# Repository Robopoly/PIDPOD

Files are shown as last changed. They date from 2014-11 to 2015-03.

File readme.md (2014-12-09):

# PIDPOD

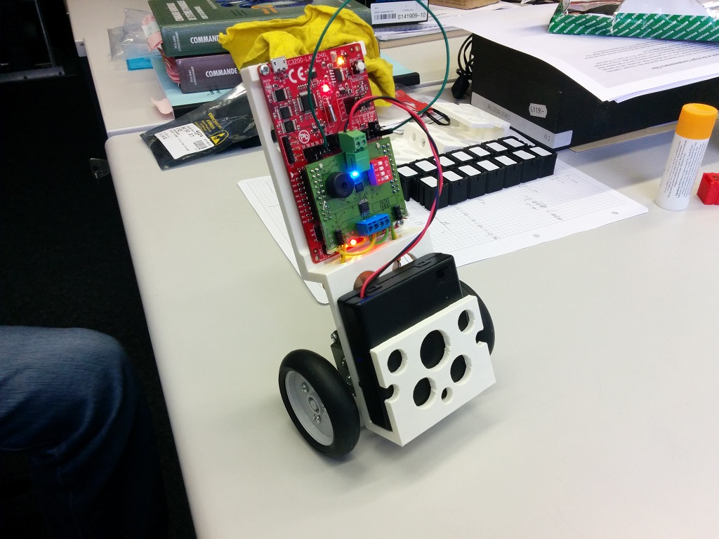
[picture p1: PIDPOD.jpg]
PIDPOD


The PIDPOD is a small self-balancing gyropod platform based on the Texas Instruments [CC3200 development board](http://www.ti.com/tool/cc3200-launchxl), a custom booster pack with additional electronics such as an inertial measurement unit (IMU) and some DC motors and wheels.

**[Watch the video of the PIDPOD in action](https://www.youtube.com/watch?v=XYrwYyiz-3s)**

## Scope statement

The PIDPOD was developed for the first Texas Instruments *Internet of Things (IoT)* workshop at [EPFL](http://www.epfl.ch/), organised by the university's robotics club: [Robopoly](http://robopoly.epfl.ch/) and [IEEE student branch](http://ieee.epfl.ch/) held on the 9th December 2014. The initiative to build the self-balancing platform was taken by Robopoly committee members and the whole project took less than 20 days from concept to product, most of the parts were readily available thanks to the robotics club parts stock.

The full scope statement was:

### Mechanical

* 2-wheeled
* 4-bay battery pack
* Upright structure
* Holes for the CC3200 development board

### Electronics (custom booster-pack)

* DRV8833 H-bridge with 100mOhm shunt resistors
* MPU9150 9-axis IMU
* Battery connector
* H-bridge connectors
* Buzzer
* 4-way DIP-switch
* LEDs
* Micromatch footprint for I2C
* Pins for input for odometry from IR sensors and encoders

### Software

* Generate PWM for motor control
* Use the on-board BMA222 accelerometer
* Interface and use the custom booster-pack IMU

### Bonus

If all main objectives from the main scope statement were satisfied before the workshop we would also implement some additional features:

* Current-control (torque) instead of voltage-control (speed) using the 100mOhm shunt and ADC
* Position control using encoders
* Set PID controller coefficients via Wi-Fi
* Interface a VGA camera (OV7670)

## Hardware

The PIDPOD uses the Tamiya double gearbox for the motors and the narrow tire set also from Tamiya, they were chosen because the were readily available at Robopoly.

For the power it uses 4 AA rechargeable batteries (4.8V total), this is partly because the LDO of the CC3200 development board requires a deltaV of 1V minimum for the 3.3V regulator and also for motor power. Although the motors should not exceed 3V we assume the system will stay at extremes for short times only.

The chassis was 3D printed on an Ultimaker 2, it's a single piece with full of holes to make the structure lighter. It holds together the electronics, motors and the battery-pack.

At first the battery pack was on top of the chassis for accessibility, but the Tamyia motors were not powerful or fast enough to stabilise the system so the battery pack was lowered to the wheel axis level, the system performed much better and the motors were definately good enough for a gyropod in this configuration.

## Electronics

The additional electonic components on the custom booster pack are: an H-bridge (DRV8833), a 9-axis IMU (MPU9150), a buzzer and a 4-way DIP-switch and various connectors.

The CC3200 development board has an accelerometer ([BMA222](http://www.bosch-sensortec.com/en/homepage/products_3/3_axis_sensors/acceleration_sensors/bma222_1/bma222)), but we found out quickly that for a good regulation a gyroscope was needed, we never succeeded in achieving stability with only an accelerometer, thus the MPU9150 on the booster pack. The MPU9150 comes in an LGA package impossible to solder by hand, thanks to the [EPFL ACI workshop](http://sti-ateliers.epfl.ch/page-19942.html), and more specifically André Badertscher, we were able solder this part with ease.

The custom booster-pack was made possible by the ACI workshop and generously manufactured thanks to Manuel Leitos, they were very kind to produce a couple PCBs for us in a very short time allowing us to make this project.

## Software

For software development we had to start by developing the PWM signal generation for motor control, we used interrupt vectors instead of hardware PWM of the CC3200 chip, in retrospective the overhead that the pin settings take is quite annoying and in an eventual next version hardware PWM should be implemented.

We found out quite fast that the on-board BMA222 accelerometer was not enough to stabilise the system, fortunately we had prepared the footprint for the MPU9150 9-axis IMU that had a 3-axis gyroscope.

By the end of the project we had a Wi-Fi enabled gyropod on which we could set the PID controller coefficients using sliders via a server running on the CC3200.

## Issues

* Stability: the PIDPOD isn't very stable as we had to hand-tune the PID coefficients because of lack of time.
* Program: the program has some non-identified erratic behaviours sometimes, we did not investigate any further as we had something that somehow worked just before the deadline.
* I2C: when the motors pulled a lot of current the I2C communication stopped with the BMC222, it turns out the traces going to the unsoldered MPU9150 were somehow affecting the bus, we brutally cut the traces and everything worked from the onwards. We used the MPU9150 IMU later on and we did not have this issue.
* Wi-Fi: sometimes when the motors pull a lot of current the Wi-Fi communication stops.
* Memory: the CC3200 had some example programs stored in the flash memory limiting the user program size to less than 50Kb, the program needed more and thus we had to find a way to use the full theoretical 256Kb. For this there was a tool to format the memory (UniFlash), but no matter what we tried the tool refused to format the chip. In the end we found out that we needed to connect the SOP2 jumpter, exactly the contrary to the formatting instructions.
* Reset: the reset button on our CC3200 development board didn't work (the button did not short when pushed), we resorted to shorting it manually with a wire when we needed a reset.
* Current-control: reading the analog values for curren-control did not work as expected so we abandoned this idea.
* Camera: there was no way to interface the camera and have all the other functionalities we needed on the custom booster-pack as it took up too many pins, so we didn't put the camera footprint on it.
* FTDI: at one point the CC3200 decided to make the PC load new drivers and enumerated as 2 serial ports, the CC3200 became impossible to reprogram via Code Composer or Energia, it was still flashable via the UniFlash tool. We fixed this issue by reflashing the FTDI chip.

# Credits

This project was developed by Marco Pagnamenta, Karl Kangur and Jean-Luc Liardon, members of the Robopoly committee and former students of EPFL.

A huge thanks to Manuel Leitos and André Badertscher from ACI workshop who made the development of the electronics possible.

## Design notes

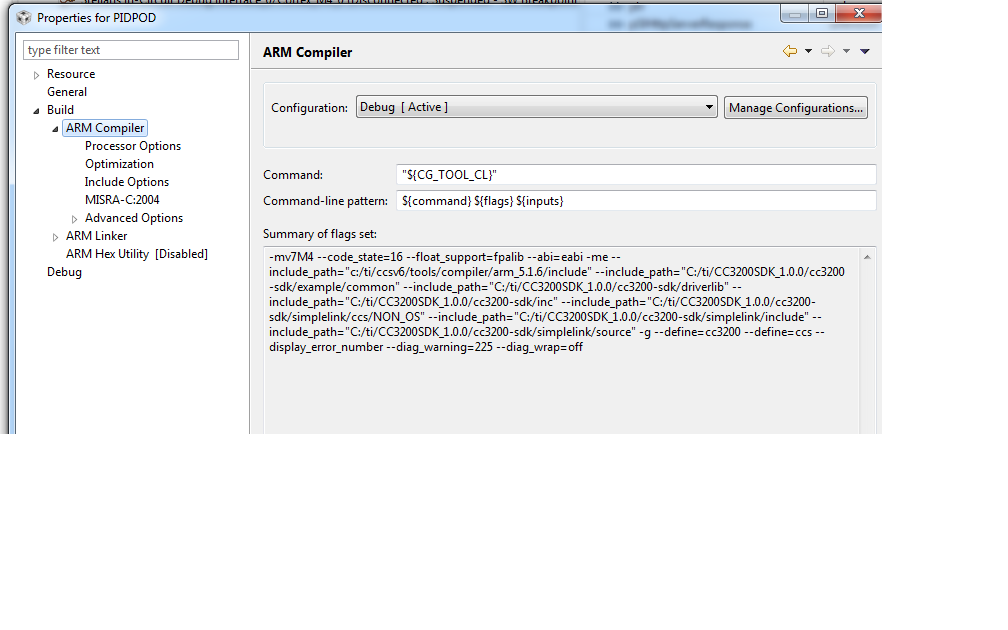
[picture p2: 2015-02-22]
CCS_project_options_screenshots/compiler_flags.png

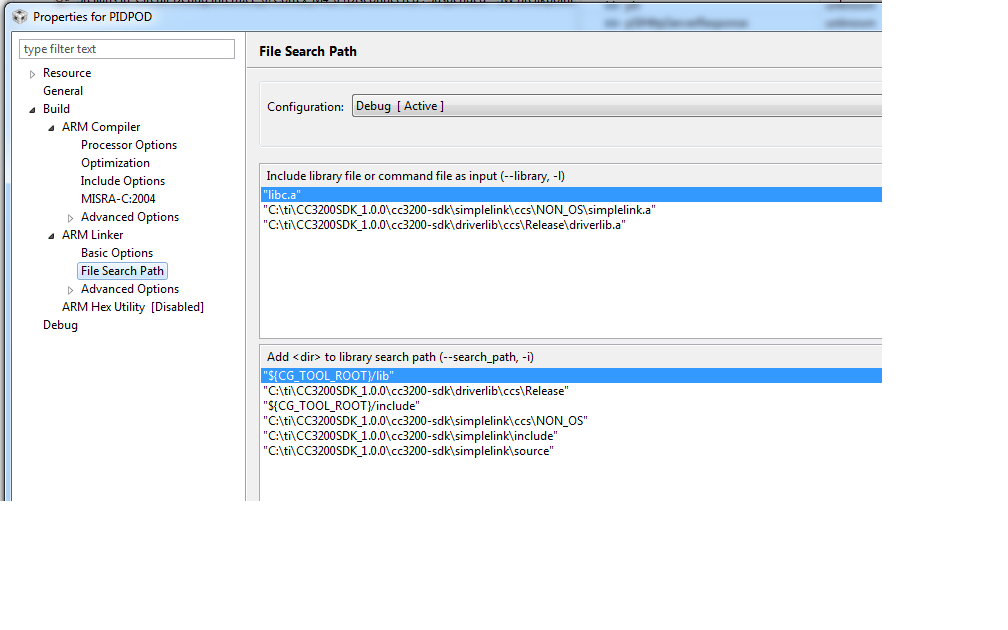
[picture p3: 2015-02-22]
CCS_project_options_screenshots/linker_search_path.png

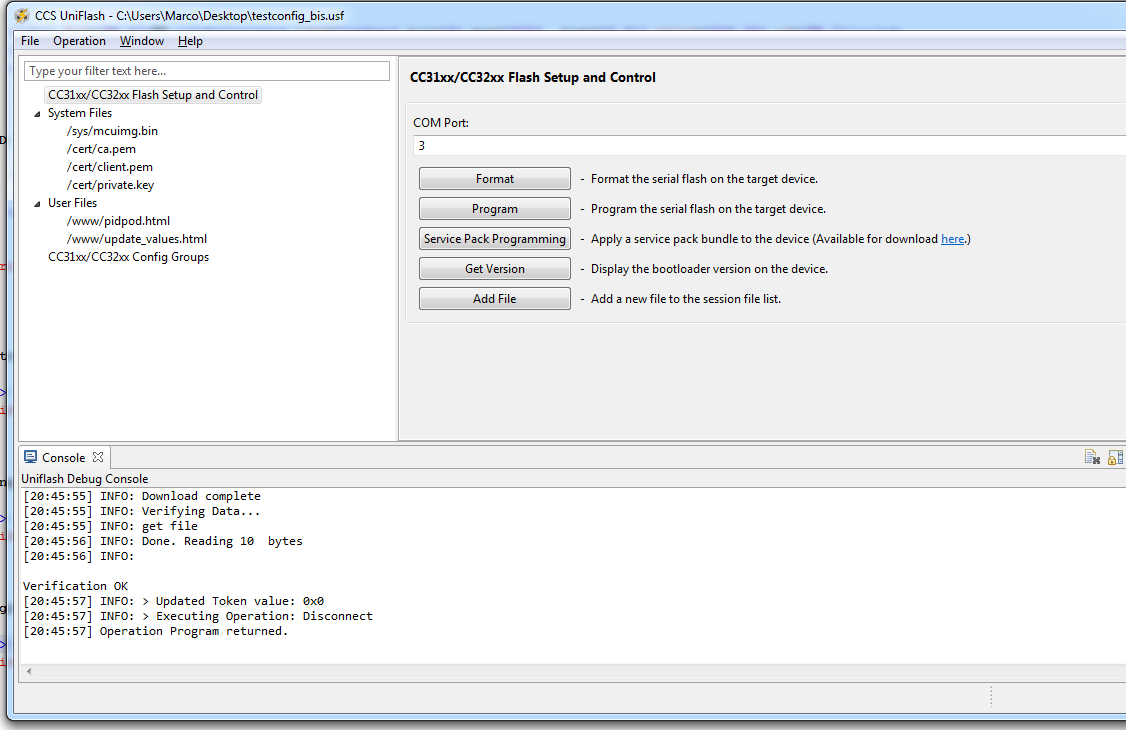
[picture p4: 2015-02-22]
CCS_project_options_screenshots/uniflash_settings.png

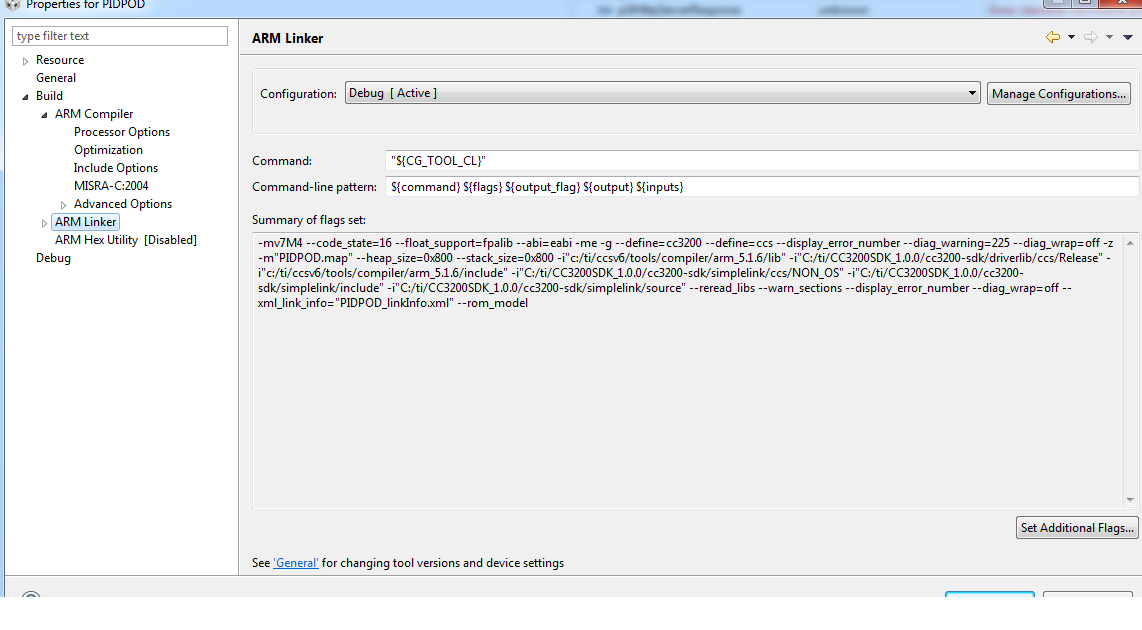
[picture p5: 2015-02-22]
CCS_project_options_screenshots/linker_flags.png

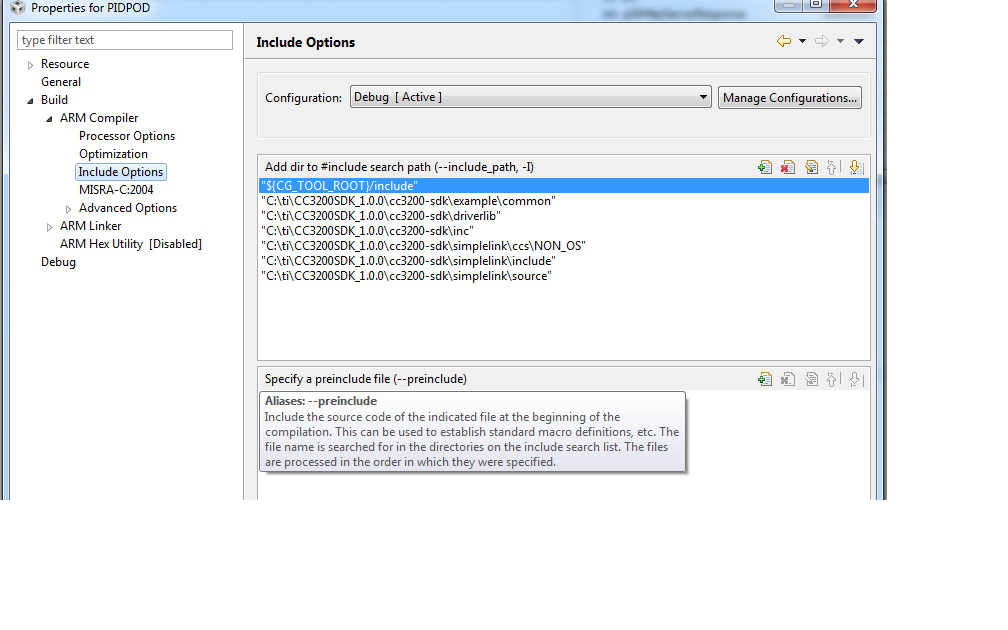
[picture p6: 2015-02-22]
CCS_project_options_screenshots/compiler_includes.png

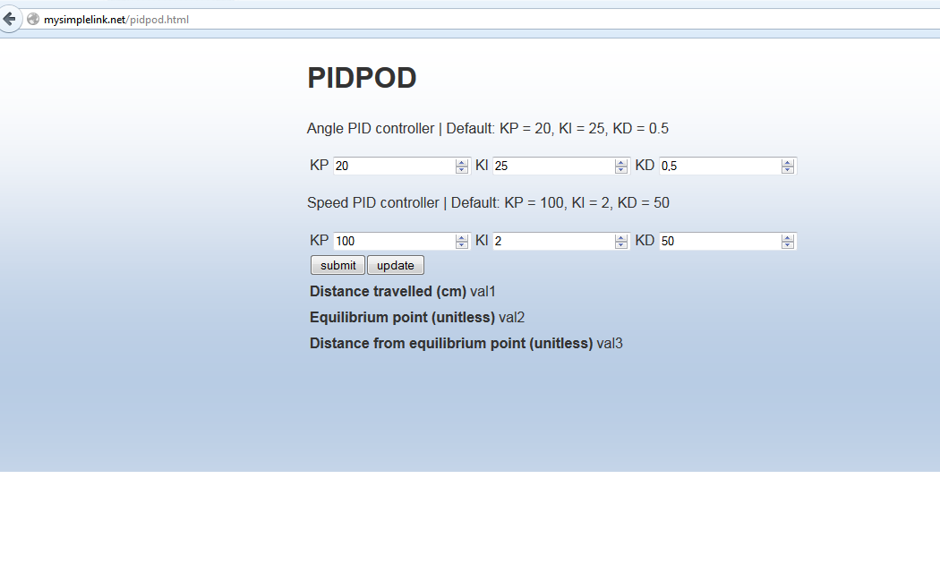
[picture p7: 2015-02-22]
CCS_project_options_screenshots/webpage.png

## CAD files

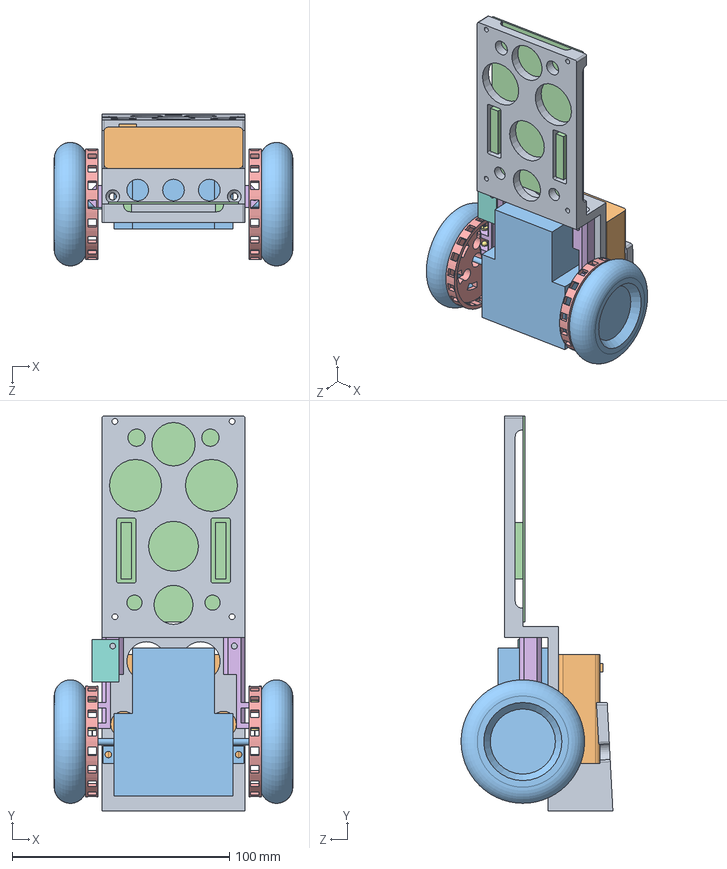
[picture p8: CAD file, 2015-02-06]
Hardware_v2/Assembly3.SLDASM
110.0 x 182.0 x 69.9 mm
Base_v3
Batteries
Wheels
CC3200
odometer3D x 2
IR_holder x 2
IR_transducer x 4
IR_PCB

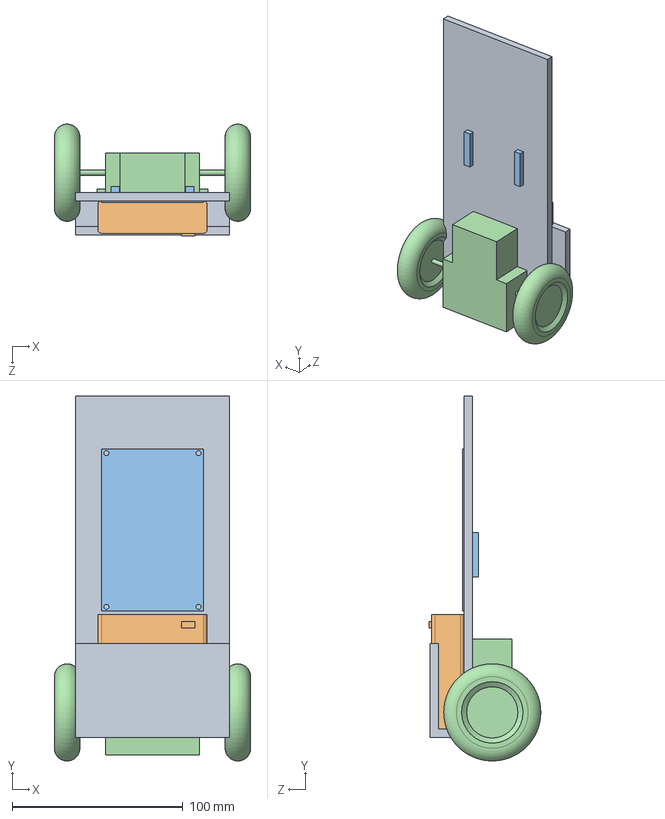
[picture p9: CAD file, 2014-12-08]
Hardware_v2/Assembly2.SLDASM
115.0 x 213.8 x 65.5 mm
Base_v2
Batteries
CC3200
Wheels

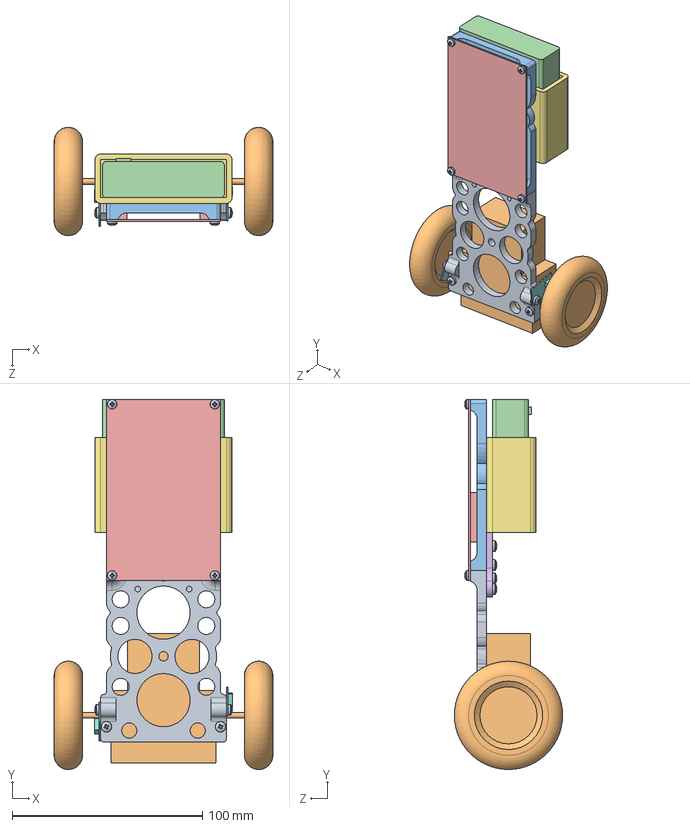
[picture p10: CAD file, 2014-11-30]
Hardware_v2/Assembly.SLDASM
115.0 x 194.5 x 56.9 mm
Base
Wheels
Top
Batteries
CC3200
Support
Battery support
ir_tcrt1000 x 2
pan head cross recess screw_iso x 15
hex nut style 1 gradeab_iso x 2
countersunk flat head cross recess screw_iso x 3

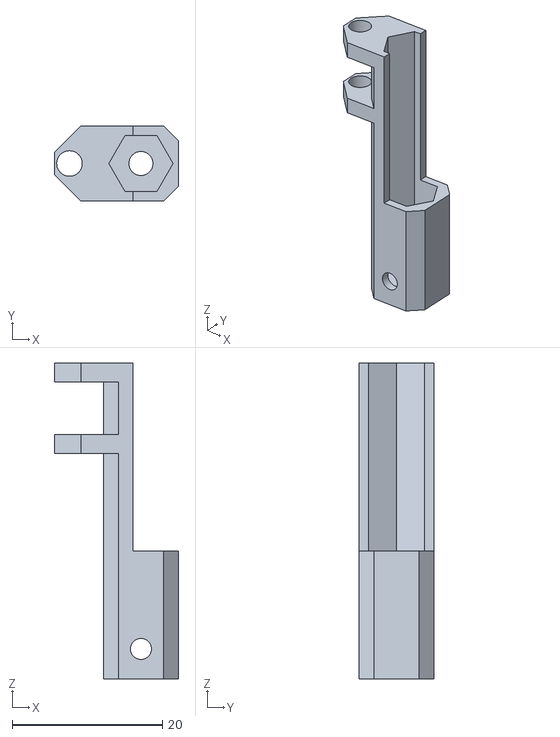
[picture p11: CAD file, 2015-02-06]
STL files/IR_holder.STL
16.5 x 10.0 x 42.0

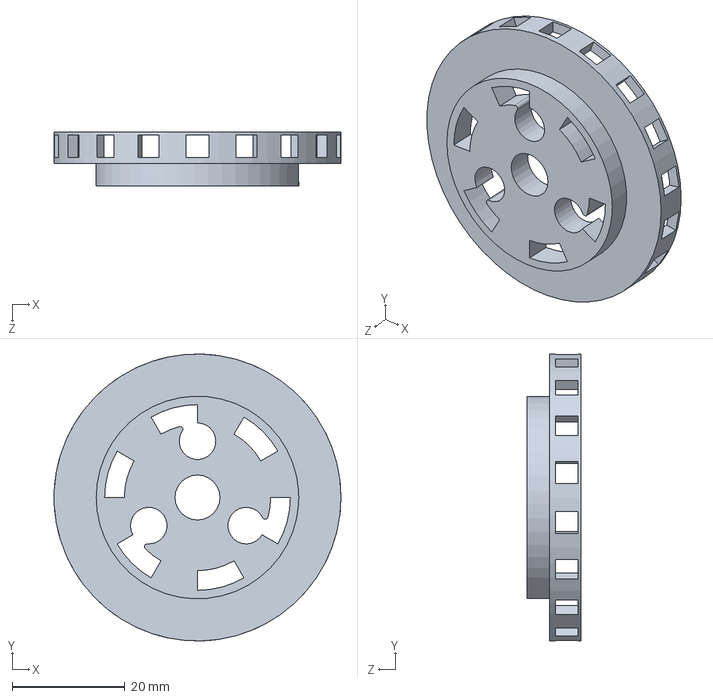
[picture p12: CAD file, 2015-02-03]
Hardware_v2/odometer3D.SLDPRT
51.0 x 51.0 x 9.60 mm

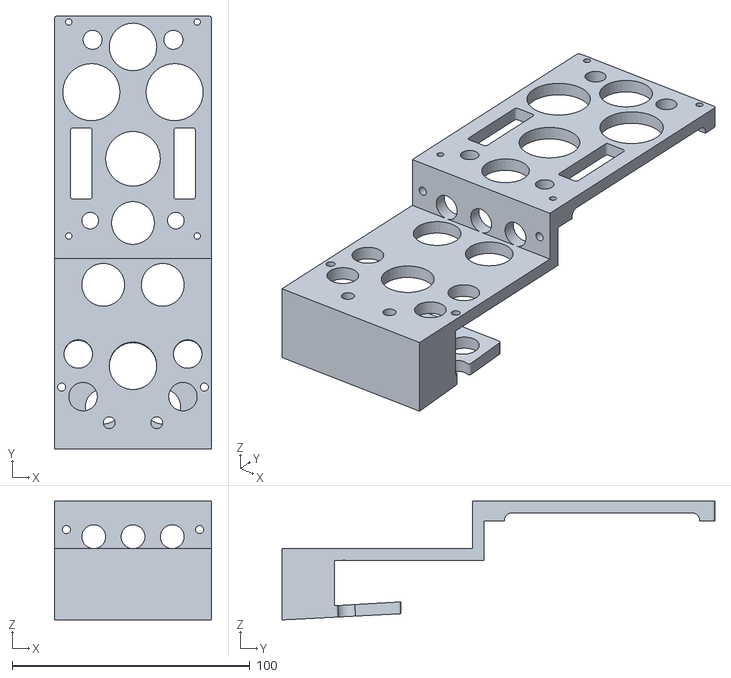
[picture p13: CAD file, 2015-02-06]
STL files/Base_v3.STL
66.0 x 182.0 x 50.0

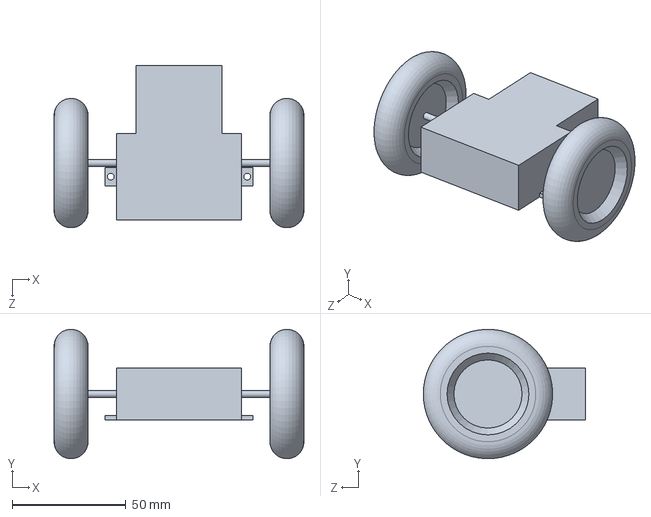
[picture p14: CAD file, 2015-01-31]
Hardware_v2/Wheels.SLDPRT
110.0 x 56.9 x 71.5 mm

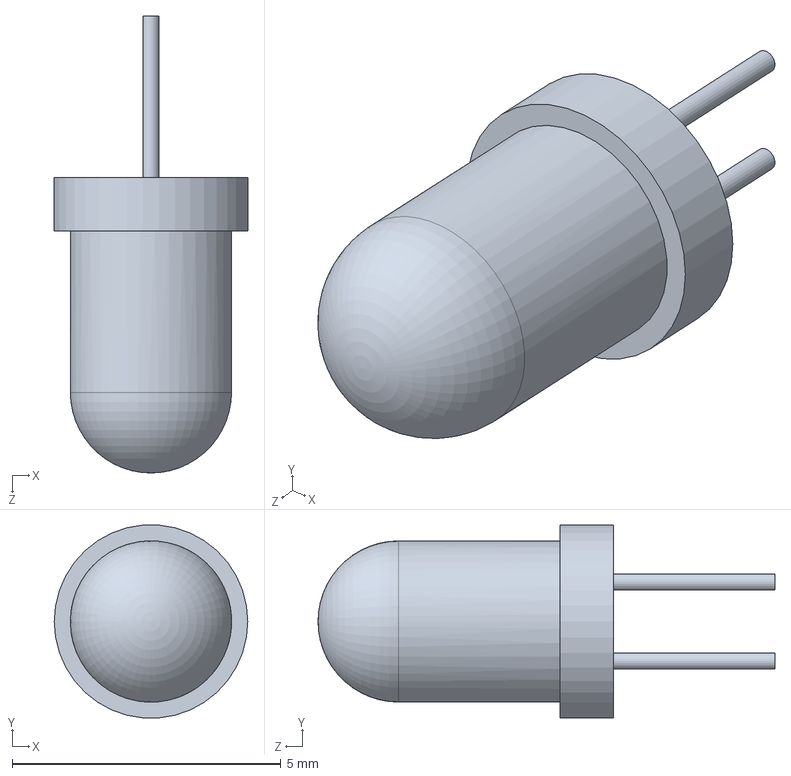
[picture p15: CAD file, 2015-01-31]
Hardware_v2/IR_transducer.SLDPRT
3.60 x 3.59 x 8.50 mm

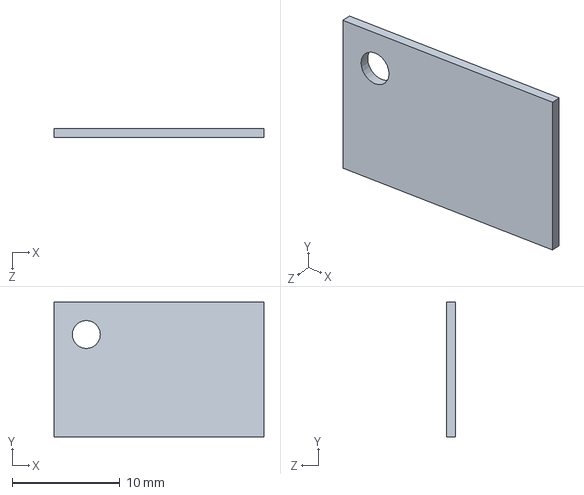
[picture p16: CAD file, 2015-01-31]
Hardware_v2/IR_PCB.SLDPRT
19.5 x 12.5 x 0.8 mm

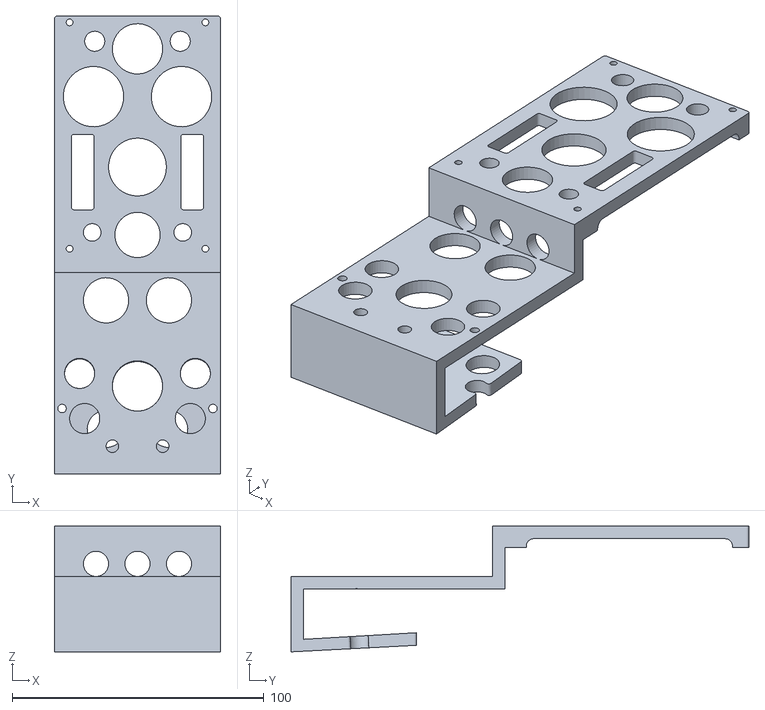
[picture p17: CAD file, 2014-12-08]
Hardware_v2/Base_v33.STL
66.0 x 182.0 x 50.0

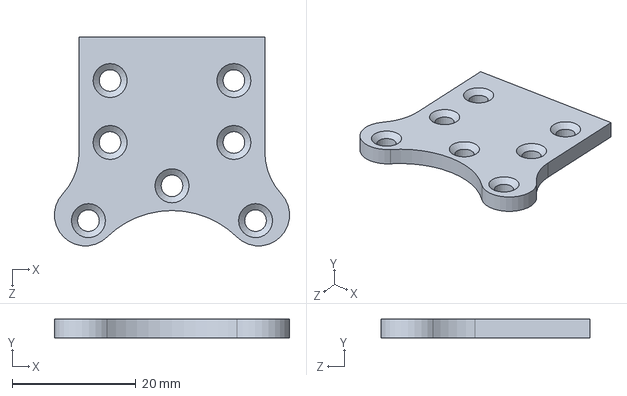
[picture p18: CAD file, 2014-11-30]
Hardware_v2/Support.SLDPRT
38.0 x 3.00 x 33.7 mm

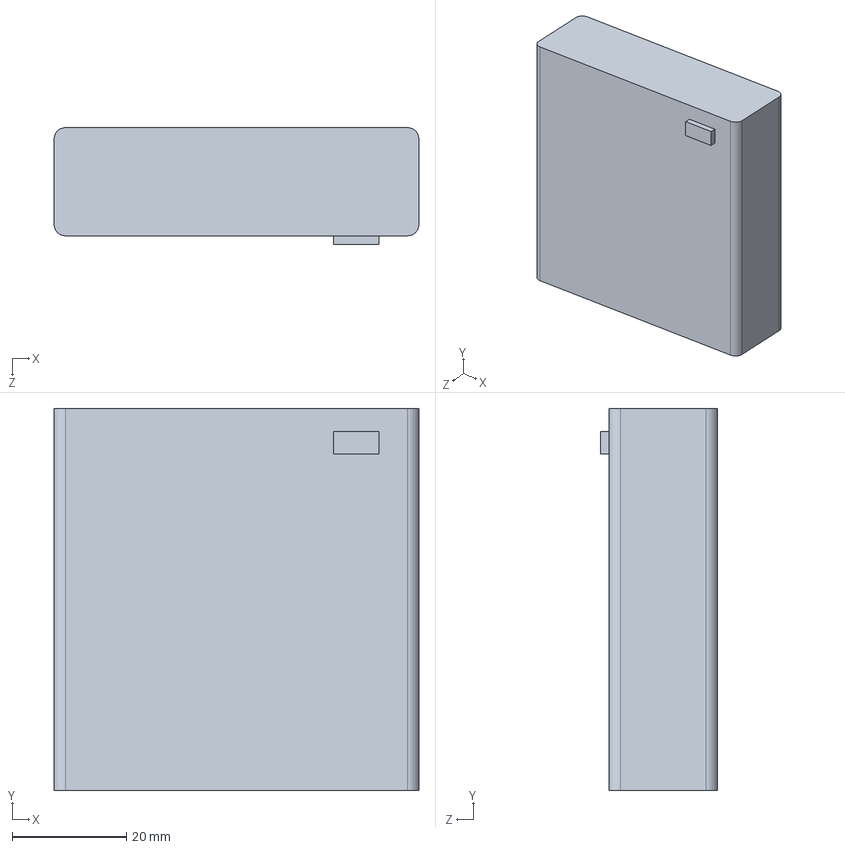
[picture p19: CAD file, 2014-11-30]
Hardware_v2/Batteries.SLDPRT
64.0 x 67.0 x 20.5 mm

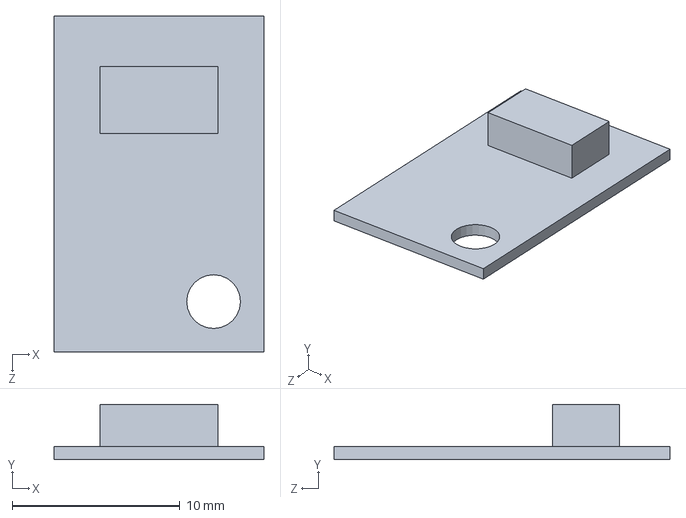
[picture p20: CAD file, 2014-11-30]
Hardware_v2/ir_tcrt1000.SLDPRT
12.5 x 3.30 x 20.0 mm

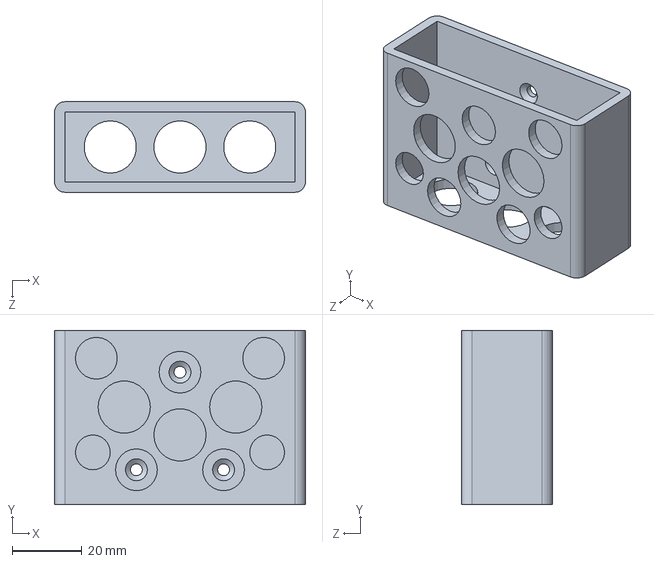
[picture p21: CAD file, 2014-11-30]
Hardware_v2/Battery support.SLDPRT
72.0 x 50.0 x 26.0 mm

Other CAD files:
Hardware_v2/IR_holder.SLDPRT
STL files/odometer3D.STL
Hardware_v2/Base_v3.SLDPRT
Hardware_v2/Top.SLDPRT
Hardware_v2/Base.SLDPRT
Hardware_v2/Base.STL
Hardware_v2/Base_v2.SLDPRT
Hardware_v2/Base_v3.STL
Hardware_v2/Battery support.STL
Hardware_v2/CC3200.SLDPRT
Hardware_v2/Support.STL
Hardware_v2/Top.STL

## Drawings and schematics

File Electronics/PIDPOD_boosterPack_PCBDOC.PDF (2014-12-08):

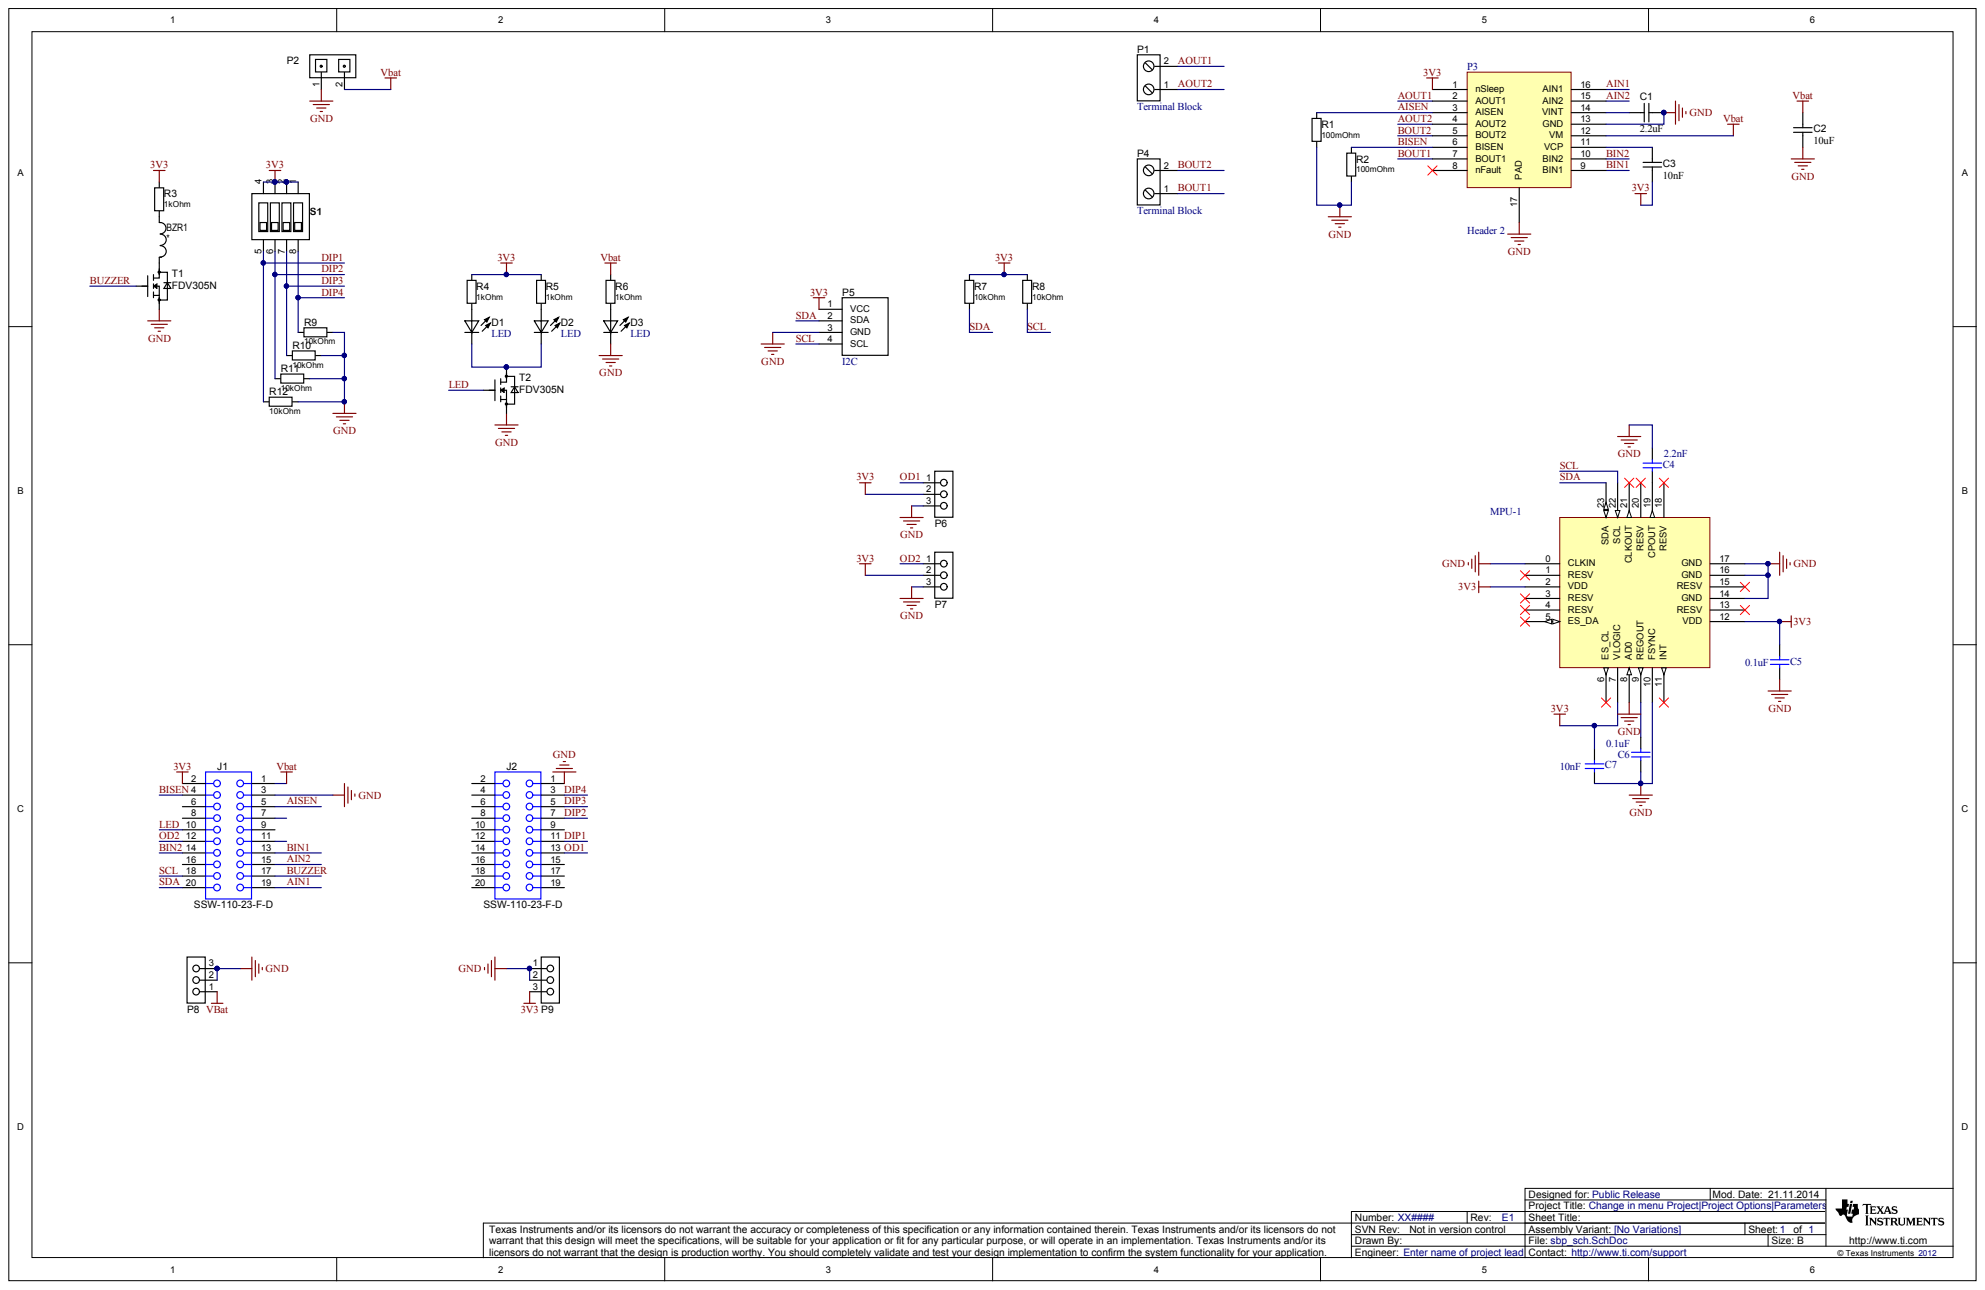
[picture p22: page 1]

DIP2
DIP3 10kOhm

RESV 18 CPOUT 19 RESV 20 CLKOUT 21 SCL 22 SDA 23

Designed for: Public Release
Project Title: Change in menu Project|Project Options|Parameters

Number: XX#### | Rev: E1 | Sheet Title:
SVN Rev: Not in version control | Assembly Variant: [No Variations] | Sheet: 1 of 1

Texas Instruments and/or its licensors do not warrant the accuracy or completeness of this specification or any information contained therein. Texas Instruments and/or its licensors do not
warrant that this design will meet the specifications, will be suitable for your application or fit for any particular purpose, or will operate in an implementation. Texas Instruments and/or its
licensors do not warrant that the design is production worthy. You should completely validate and test your design implementation to confirm the system functionality for your application.

Drawn By:
Engineer: Enter name of project lead

sbp_sch.SchDoc
File:
Contact: http://www.ti.com/support

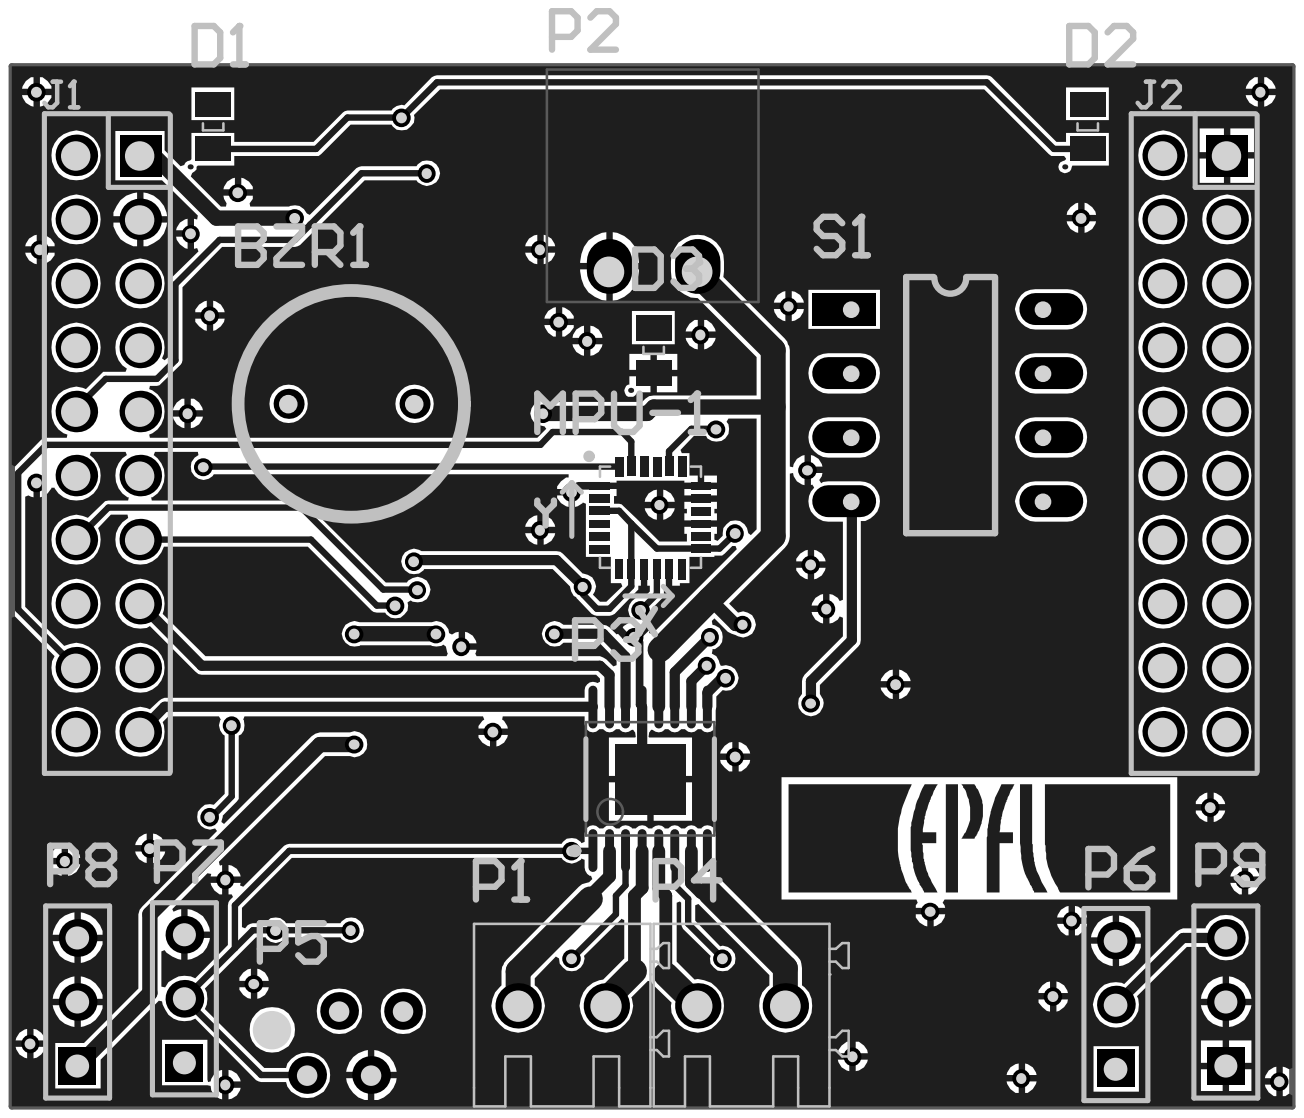
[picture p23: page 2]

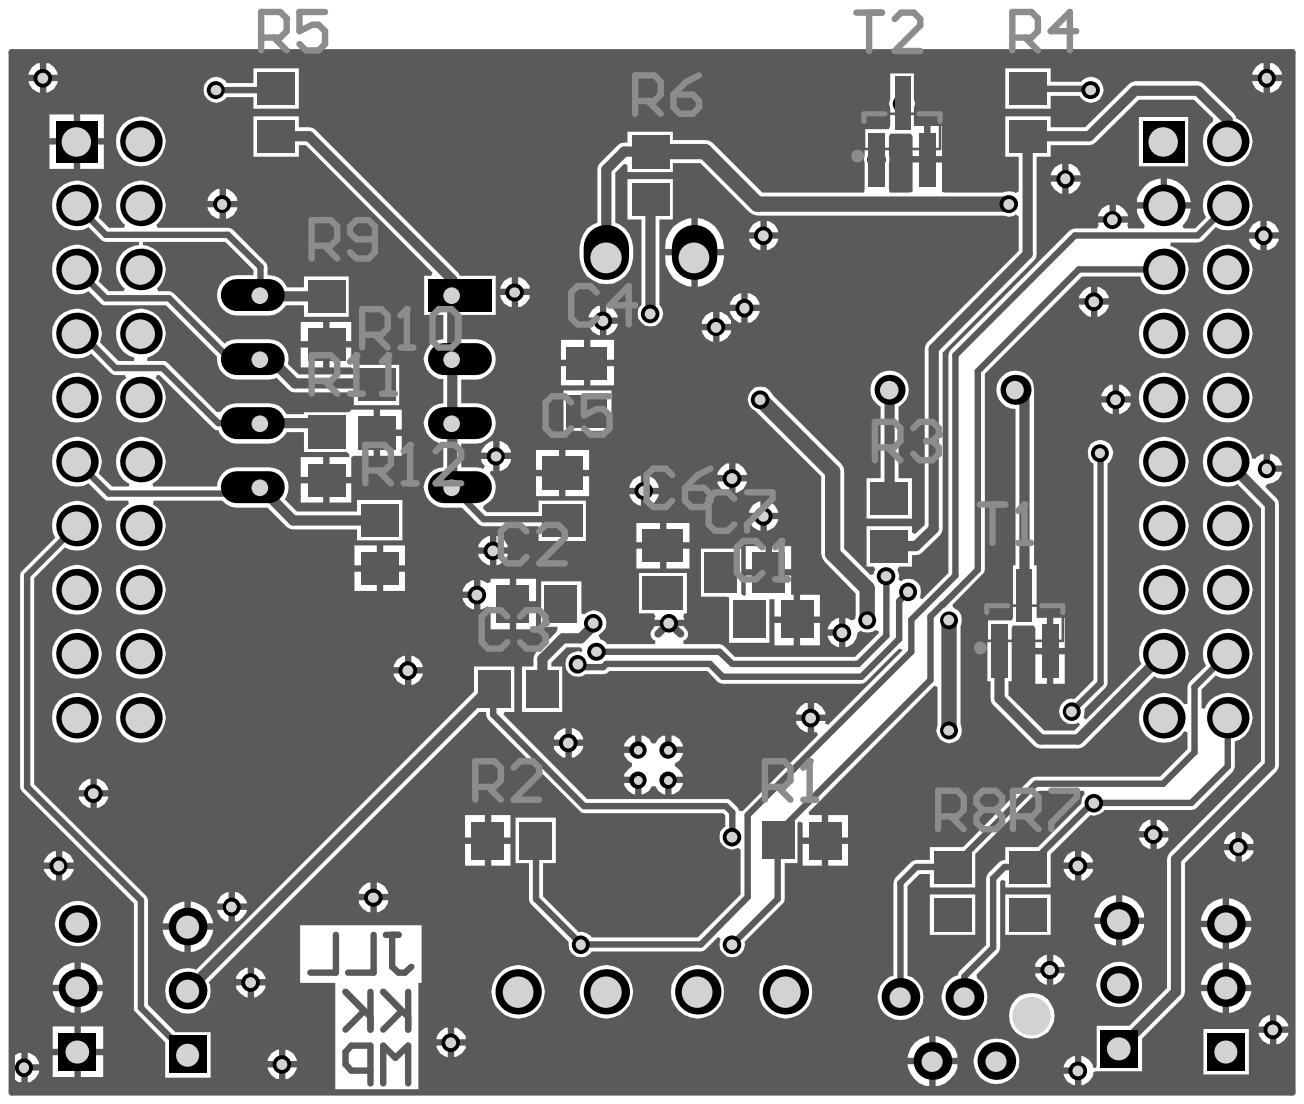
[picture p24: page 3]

Quantit y | Comment | LibRef | Designator | Description | Footprint
1 | | L | BZR1 | | L_4_7uH
1 | C1 | C | C1 | Capacitor | C/0805
1 | C3 | C | C2 | Capacitor | C/0805
1 | C2 | C | C3 | Capacitor | C/0805
4 | C0805 | C0805 | C4, C5, C6, C7 | Ceramic Chip Capacitor -Standard | MELF-R2012-0805
3 | LED | LED | D1, D2, D3 | | LED-2012[0805]
2 | SSW-110-23-F-D | SSW-110-23-F-D | J1, J2 | Connector, Receptacle, 100mil, 10x2, Gold plated, TH | CONN_SSW-110-23-F-D
1 | 9-axis | MPU-9150 | MPU-1 | 9-axis sensor (gyroscope, accelerometre, magnétomètre) | MPU-9150
2 | Terminal Block | Screw Block 2 | P1, P4 | 2-Pin Screw Terminal | Phoenix PT 2-Pole
1 | MC 1,5/ 2-G-3,5 | Phoenix MC 2 | P2 | Female jack 3.5mm for screw-in connectors | Phoenix MC 2-Pole
1 | Header 2 | DRV8833PWPR | P3 | Header, 2-Pin | DRV8833PWPR
1 | I2C | Micromatch-I2C | P5 | Micromatch I2C Connector | TYCO/215079-4
4 | Header 3 | Header 3 | P6, P7, P8, P9 | Header, 3-Pin | HEADER1x3
2 | 100mOhm | R | R1, R2 | Resistor | R/0805
4 | 1kOhm | R | R3, R4, R5, R6 | Resistor | R/0805
6 | 10kOhm | R | R7, R8, R9, R10, R11, R12 | Resistor | R/0805
1 | DIP SW 4 | DIP Switch 4 | S1 | 8/16 bit Microcontroller | DIP SW 8
2 | FDV305N | T/FDV305N | T1, T2 | MOSFET N SOT-23 20V 220mOhm | SOT23-3

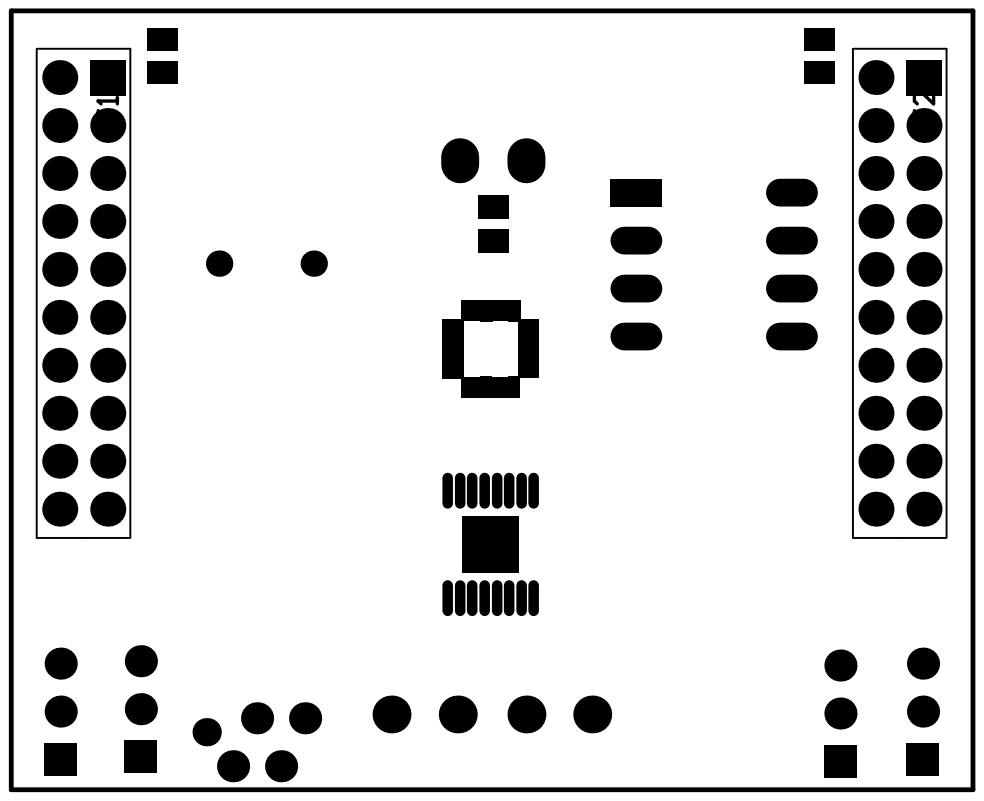
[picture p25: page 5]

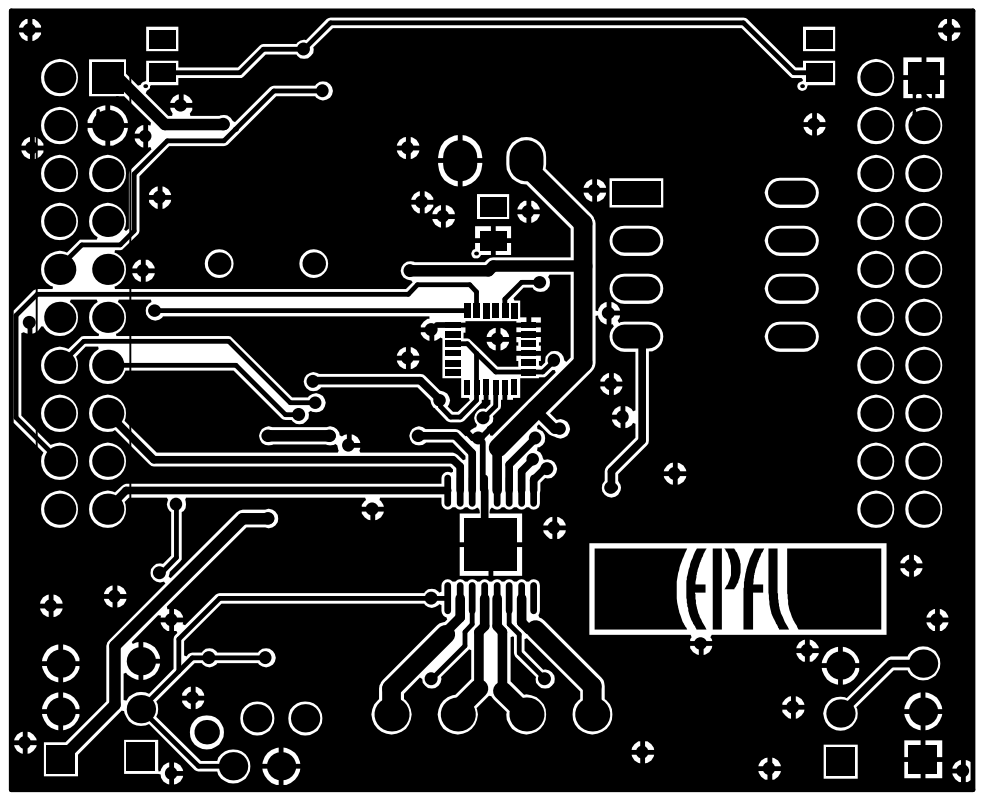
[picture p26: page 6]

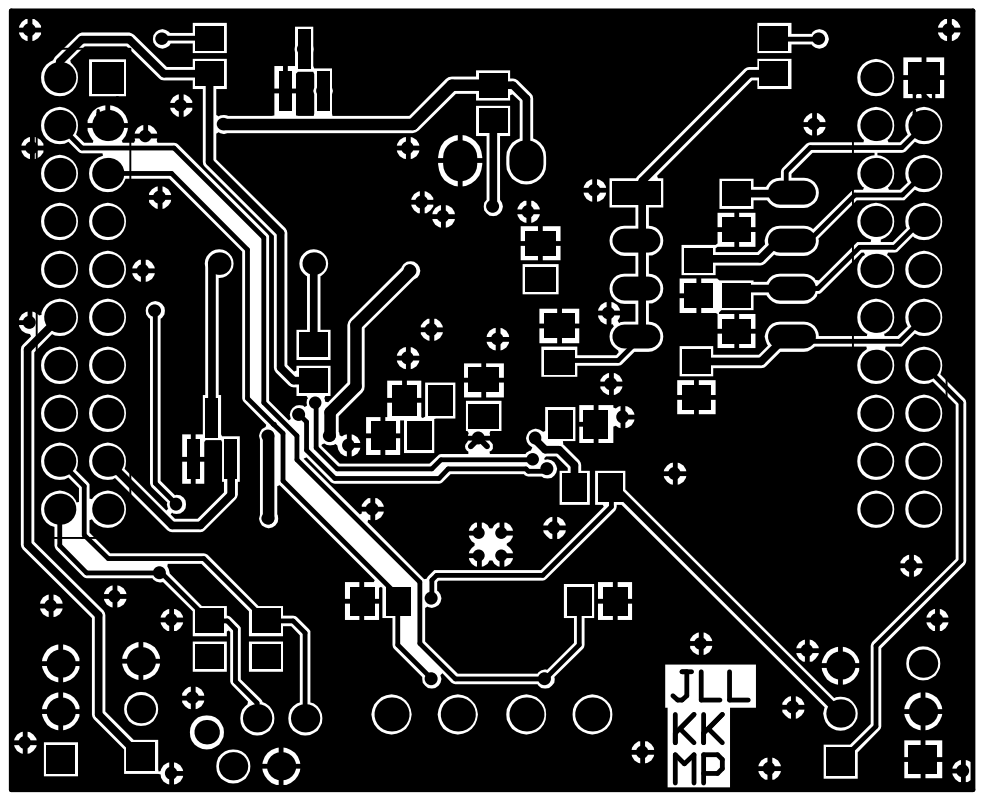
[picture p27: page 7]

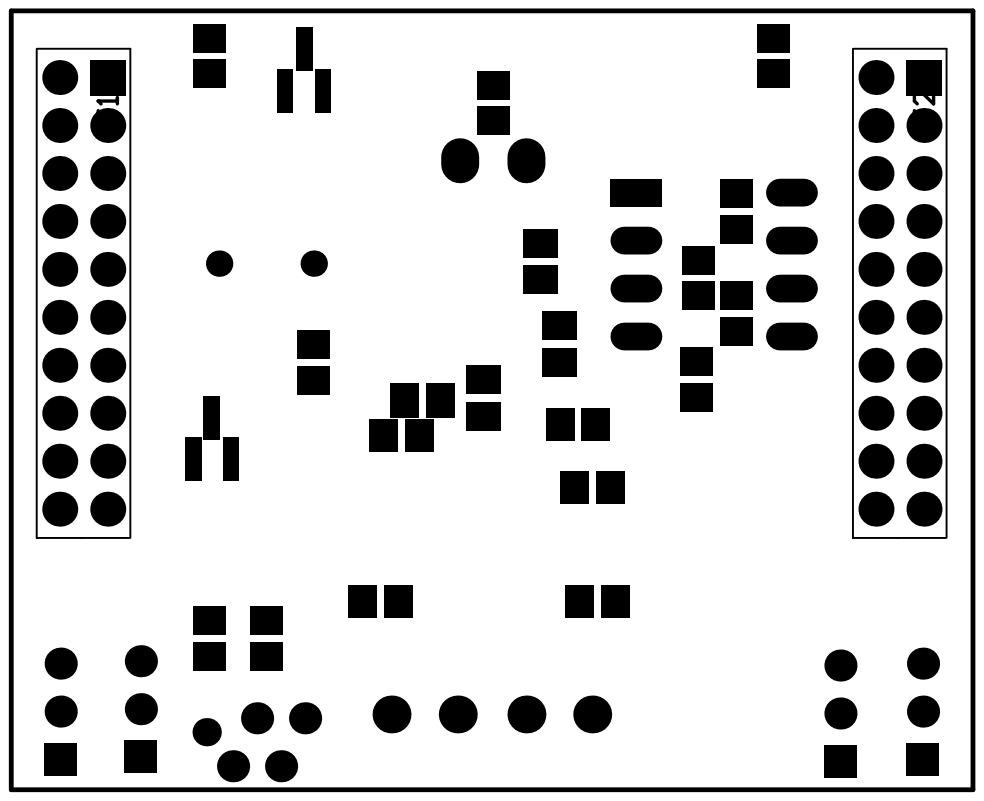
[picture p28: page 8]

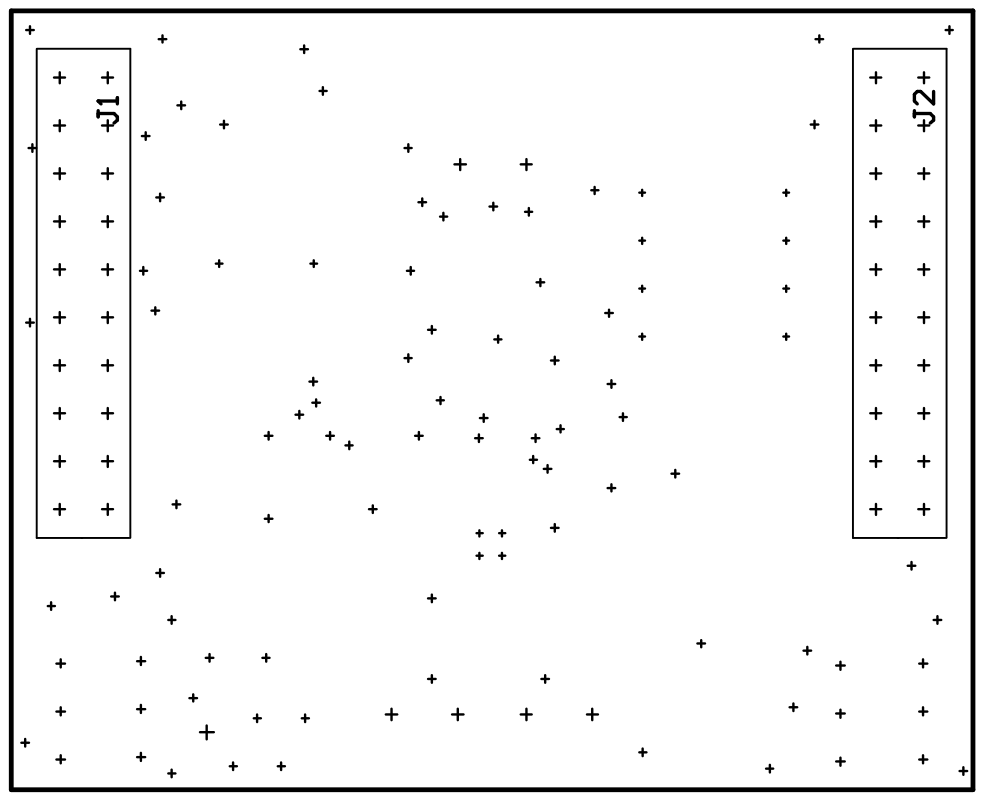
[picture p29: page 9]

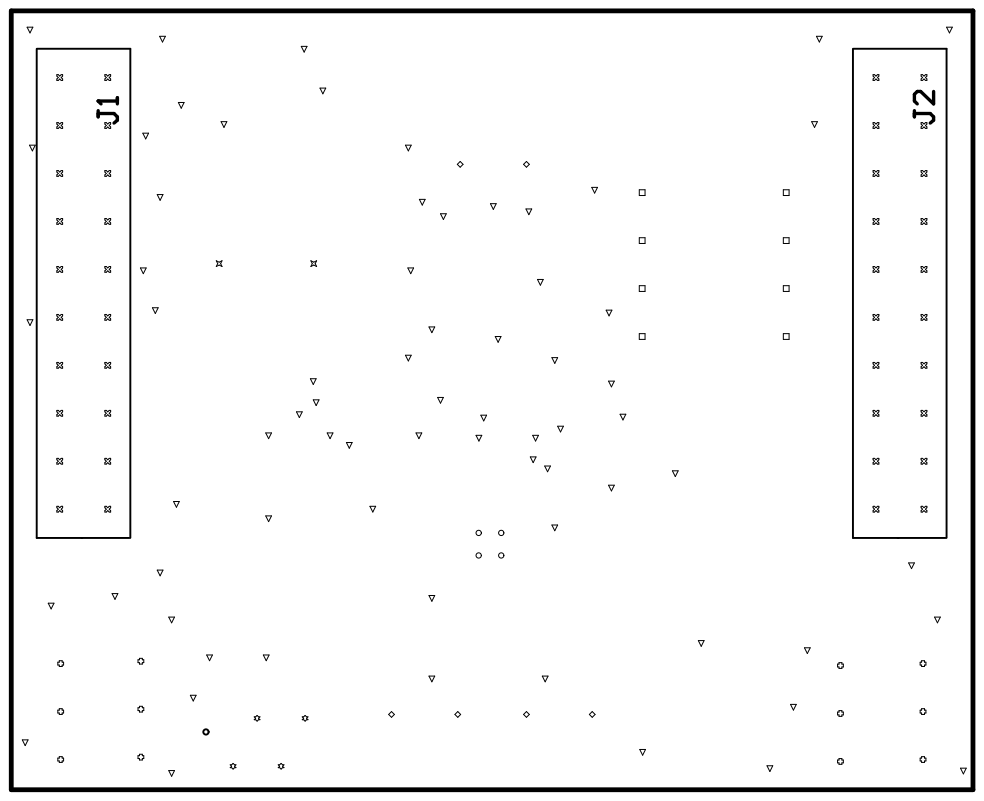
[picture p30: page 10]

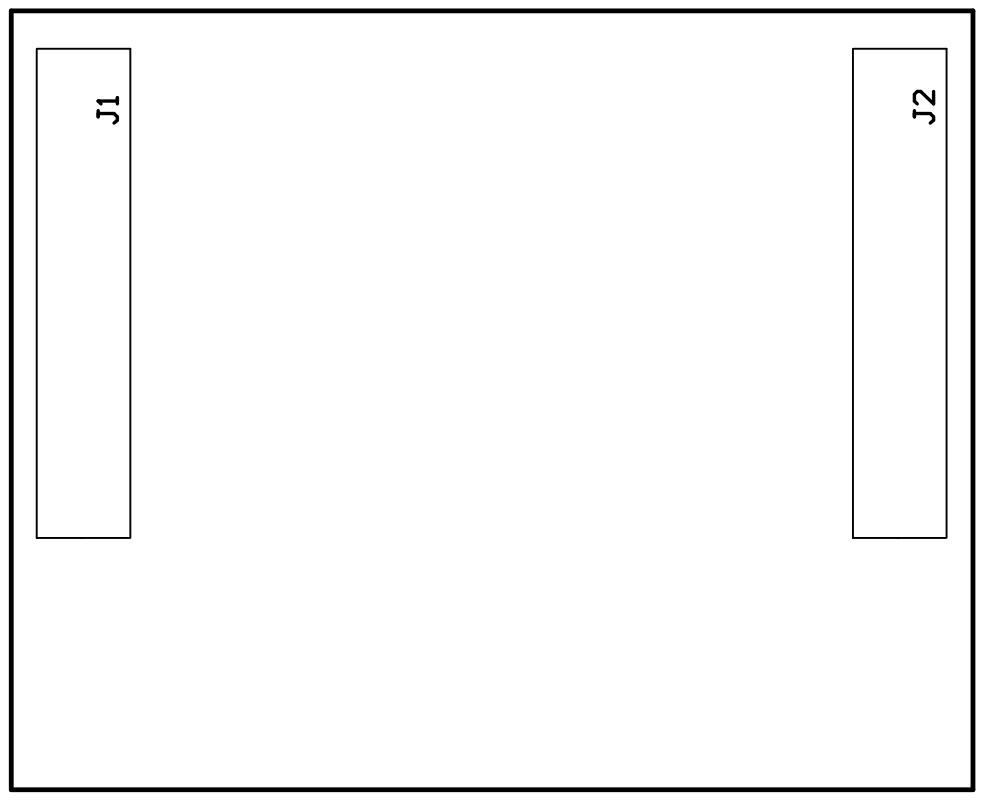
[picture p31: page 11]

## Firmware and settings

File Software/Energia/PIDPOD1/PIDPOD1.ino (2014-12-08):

/*
 * Name:        PIDPOD
 * Date:        2014-11-28
 * Version:     1.0
 * Description: Segway-type self-balancing robot sketch based on the CC3200 development board.
 */

//#define ENABLE_MOTORS
 

#include <Wire.h>

// Register names according to the datasheet.
// According to the InvenSense document
// "MPU-9150 Register Map and Descriptions Revision 4.0",

#define MPU9150_SELF_TEST_X        0x0D   // R/W
#define MPU9150_SELF_TEST_Y        0x0E   // R/W
#define MPU9150_SELF_TEST_X        0x0F   // R/W
#define MPU9150_SELF_TEST_A        0x10   // R/W
#define MPU9150_SMPLRT_DIV         0x19   // R/W
#define MPU9150_CONFIG             0x1A   // R/W
#define MPU9150_GYRO_CONFIG        0x1B   // R/W
#define MPU9150_ACCEL_CONFIG       0x1C   // R/W
#define MPU9150_FF_THR             0x1D   // R/W
#define MPU9150_FF_DUR             0x1E   // R/W
#define MPU9150_MOT_THR            0x1F   // R/W
#define MPU9150_MOT_DUR            0x20   // R/W
#define MPU9150_ZRMOT_THR          0x21   // R/W
#define MPU9150_ZRMOT_DUR          0x22   // R/W
#define MPU9150_FIFO_EN            0x23   // R/W
#define MPU9150_I2C_MST_CTRL       0x24   // R/W
#define MPU9150_I2C_SLV0_ADDR      0x25   // R/W
#define MPU9150_I2C_SLV0_REG       0x26   // R/W
#define MPU9150_I2C_SLV0_CTRL      0x27   // R/W
#define MPU9150_I2C_SLV1_ADDR      0x28   // R/W
#define MPU9150_I2C_SLV1_REG       0x29   // R/W
#define MPU9150_I2C_SLV1_CTRL      0x2A   // R/W
#define MPU9150_I2C_SLV2_ADDR      0x2B   // R/W
#define MPU9150_I2C_SLV2_REG       0x2C   // R/W
#define MPU9150_I2C_SLV2_CTRL      0x2D   // R/W
#define MPU9150_I2C_SLV3_ADDR      0x2E   // R/W
#define MPU9150_I2C_SLV3_REG       0x2F   // R/W
#define MPU9150_I2C_SLV3_CTRL      0x30   // R/W
#define MPU9150_I2C_SLV4_ADDR      0x31   // R/W
#define MPU9150_I2C_SLV4_REG       0x32   // R/W
#define MPU9150_I2C_SLV4_DO        0x33   // R/W
#define MPU9150_I2C_SLV4_CTRL      0x34   // R/W
#define MPU9150_I2C_SLV4_DI        0x35   // R  
#define MPU9150_I2C_MST_STATUS     0x36   // R
#define MPU9150_INT_PIN_CFG        0x37   // R/W
#define MPU9150_INT_ENABLE         0x38   // R/W
#define MPU9150_INT_STATUS         0x3A   // R  
#define MPU9150_ACCEL_XOUT_H       0x3B   // R  
#define MPU9150_ACCEL_XOUT_L       0x3C   // R  
#define MPU9150_ACCEL_YOUT_H       0x3D   // R  
#define MPU9150_ACCEL_YOUT_L       0x3E   // R  
#define MPU9150_ACCEL_ZOUT_H       0x3F   // R  
#define MPU9150_ACCEL_ZOUT_L       0x40   // R  
#define MPU9150_TEMP_OUT_H         0x41   // R  
#define MPU9150_TEMP_OUT_L         0x42   // R  
#define MPU9150_GYRO_XOUT_H        0x43   // R  
#define MPU9150_GYRO_XOUT_L        0x44   // R  
#define MPU9150_GYRO_YOUT_H        0x45   // R  
#define MPU9150_GYRO_YOUT_L        0x46   // R  
#define MPU9150_GYRO_ZOUT_H        0x47   // R  
#define MPU9150_GYRO_ZOUT_L        0x48   // R  
#define MPU9150_EXT_SENS_DATA_00   0x49   // R  
#define MPU9150_EXT_SENS_DATA_01   0x4A   // R  
#define MPU9150_EXT_SENS_DATA_02   0x4B   // R  
#define MPU9150_EXT_SENS_DATA_03   0x4C   // R  
#define MPU9150_EXT_SENS_DATA_04   0x4D   // R  
#define MPU9150_EXT_SENS_DATA_05   0x4E   // R  
#define MPU9150_EXT_SENS_DATA_06   0x4F   // R  
#define MPU9150_EXT_SENS_DATA_07   0x50   // R  
#define MPU9150_EXT_SENS_DATA_08   0x51   // R  
#define MPU9150_EXT_SENS_DATA_09   0x52   // R  
#define MPU9150_EXT_SENS_DATA_10   0x53   // R  
#define MPU9150_EXT_SENS_DATA_11   0x54   // R  
#define MPU9150_EXT_SENS_DATA_12   0x55   // R  
#define MPU9150_EXT_SENS_DATA_13   0x56   // R  
#define MPU9150_EXT_SENS_DATA_14   0x57   // R  
#define MPU9150_EXT_SENS_DATA_15   0x58   // R  
#define MPU9150_EXT_SENS_DATA_16   0x59   // R  
#define MPU9150_EXT_SENS_DATA_17   0x5A   // R  
#define MPU9150_EXT_SENS_DATA_18   0x5B   // R  
#define MPU9150_EXT_SENS_DATA_19   0x5C   // R  
#define MPU9150_EXT_SENS_DATA_20   0x5D   // R  
#define MPU9150_EXT_SENS_DATA_21   0x5E   // R  
#define MPU9150_EXT_SENS_DATA_22   0x5F   // R  
#define MPU9150_EXT_SENS_DATA_23   0x60   // R  
#define MPU9150_MOT_DETECT_STATUS  0x61   // R  
#define MPU9150_I2C_SLV0_DO        0x63   // R/W
#define MPU9150_I2C_SLV1_DO        0x64   // R/W
#define MPU9150_I2C_SLV2_DO        0x65   // R/W
#define MPU9150_I2C_SLV3_DO        0x66   // R/W
#define MPU9150_I2C_MST_DELAY_CTRL 0x67   // R/W
#define MPU9150_SIGNAL_PATH_RESET  0x68   // R/W
#define MPU9150_MOT_DETECT_CTRL    0x69   // R/W
#define MPU9150_USER_CTRL          0x6A   // R/W
#define MPU9150_PWR_MGMT_1         0x6B   // R/W
#define MPU9150_PWR_MGMT_2         0x6C   // R/W
#define MPU9150_FIFO_COUNTH        0x72   // R/W
#define MPU9150_FIFO_COUNTL        0x73   // R/W
#define MPU9150_FIFO_R_W           0x74   // R/W
#define MPU9150_WHO_AM_I           0x75   // R

//MPU9150 Compass
#define MPU9150_CMPS_XOUT_L        0x4A   // R
#define MPU9150_CMPS_XOUT_H        0x4B   // R
#define MPU9150_CMPS_YOUT_L        0x4C   // R
#define MPU9150_CMPS_YOUT_H        0x4D   // R
#define MPU9150_CMPS_ZOUT_L        0x4E   // R
#define MPU9150_CMPS_ZOUT_H        0x4F   // R

// I2C address 0x69 could be 0x68 depends on your wiring. 
int MPU9150_I2C_ADDRESS = 0x68;

//Variables where our values can be stored
int cmps[3];
int accl[3];
int gyro[3];
int temp;

#include <inc/hw_types.h>
#include <inc/hw_timer.h>
#include <driverlib/prcm.h>
#include <driverlib/timer.h>
//#include <driverlib/adc.h>

#define MOTOR_PRESCALER 8000
#define MOTOR_OFFSET 400
#define AVG  50

int8_t speedLeft = 0;
int8_t speedRight = 0;

int16_t speed = 0;
int16_t error = 0;
int16_t memory[AVG];
int16_t error_avg = 0;
int16_t integral = 0;
int16_t derivate = 0;

uint8_t i,j;

// Includes for BMA222 accelerometer communication
//#include <Wire.h>
//#include <BMA222.h>

// Wi-Fi server stuff
/*#include <SPI.h>
#include <WiFi.h>
#include <WiFiClient.h>
#include <WiFiServer.h>*/

// server instance
//WiFiServer server(80);

// PID coefficients
#define UPRIGHT_VALUE_ACCELEROMETER 22
#define KP 6.
#define KI 0.
#define KD 0.

//BMA222 accelerometer;

// Pin definitions
#define LED RED_LED
#define AIN1x	30
#define AIN2x	28
#define BIN1x	8
#define BIN2x	7
#define AISEN	23
#define BISEN	2

uint8_t bitA1, bitA2, bitB1, bitB2;
uint8_t portA1, portA2, portB1, portB2;
uint32_t baseA1, baseA2, baseB1, baseB2;

// your network name also called SSID
char ssid[] = "networkname";
// your network password
char password[] = "password";
// your network key Index number (needed only for WEP)
int keyIndex = 0;

void motorSetup()
{
  pinMode(AIN1x, OUTPUT);
  pinMode(AIN2x, OUTPUT);
  pinMode(BIN1x, OUTPUT);
  pinMode(BIN2x, OUTPUT);

  bitA1 = digitalPinToBitMask(AIN1x);
  bitA2 = digitalPinToBitMask(AIN2x);
  bitB1 = digitalPinToBitMask(BIN1x);
  bitB2 = digitalPinToBitMask(BIN2x);
  
  portA1 = digitalPinToPort(AIN1x);
  portA2 = digitalPinToPort(AIN2x);
  portB1 = digitalPinToPort(BIN1x);
  portB2 = digitalPinToPort(BIN2x);
  
  baseA1 = (uint32_t) portBASERegister(portA1);
  baseA2 = (uint32_t) portBASERegister(portA2);
  baseB1 = (uint32_t) portBASERegister(portB1);
  baseB2 = (uint32_t) portBASERegister(portB2);
  
  // Enable timer A peripheral
  MAP_PRCMPeripheralClkEnable(PRCM_TIMERA0, PRCM_RUN_MODE_CLK);
  MAP_PRCMPeripheralReset(PRCM_TIMERA0);
  
  // Split channels and configure for periodic interrupts
  MAP_TimerConfigure(TIMERA0_BASE, TIMER_CFG_SPLIT_PAIR | TIMER_CFG_A_PERIODIC | TIMER_CFG_B_PERIODIC);
  MAP_TimerPrescaleSet(TIMERA0_BASE,TIMER_A,0);
  MAP_TimerPrescaleSet(TIMERA0_BASE,TIMER_B,0);

  // Set compare interrupt
  MAP_TimerIntEnable(TIMERA0_BASE, TIMER_TIMA_MATCH);
  MAP_TimerIntEnable(TIMERA0_BASE, TIMER_TIMB_MATCH);

  // Configure compare interrupt, start with 0 speed
  MAP_TimerMatchSet(TIMERA0_BASE, TIMER_A, 0);
  MAP_TimerMatchSet(TIMERA0_BASE, TIMER_B, 0);

  // Set timeout interrupt
  MAP_TimerIntRegister(TIMERA0_BASE, TIMER_A, TimerBaseIntHandlerA);
  MAP_TimerIntRegister(TIMERA0_BASE, TIMER_B, TimerBaseIntHandlerB);
  MAP_TimerIntEnable(TIMERA0_BASE, TIMER_TIMA_TIMEOUT);
  MAP_TimerIntEnable(TIMERA0_BASE, TIMER_TIMB_TIMEOUT);

  // Turn on timers
  MAP_TimerLoadSet(TIMERA0_BASE, TIMER_A, MOTOR_PRESCALER);
  MAP_TimerLoadSet(TIMERA0_BASE, TIMER_B, MOTOR_PRESCALER);
 
  MAP_TimerEnable(TIMERA0_BASE, TIMER_A);
  MAP_TimerEnable(TIMERA0_BASE, TIMER_B);
}

void TimerBaseIntHandlerA(void)
{
  if(HWREG(TIMERA0_BASE + TIMER_O_MIS) & 0x10)
  {
    // Match interrupt
    HWREG(TIMERA0_BASE + TIMER_O_ICR) = 0x10;
    if(speedLeft > 0)
    {
      MAP_GPIOPinWrite(baseA1, bitA1, 0);
      MAP_GPIOPinWrite(baseA2, bitA2, bitA2);
    }
    else
    {
      MAP_GPIOPinWrite(baseA1, bitA1, bitA1);
      MAP_GPIOPinWrite(baseA2, bitA2, 0);
    }
  }
  else
  {
    // Overflow interrupt
    HWREG(TIMERA0_BASE + TIMER_O_ICR) = 0x1;
    MAP_GPIOPinWrite(baseA1, bitA1, bitA1);
    MAP_GPIOPinWrite(baseA2, bitA2, bitA2);
  }
}

void TimerBaseIntHandlerB(void)
{
  if(HWREG(TIMERA0_BASE + TIMER_O_MIS) & 0x800)
  {
    // Match interrupt
    HWREG(TIMERA0_BASE + TIMER_O_ICR) = 0x800;
    if(speedRight > 0)
    {
      MAP_GPIOPinWrite(baseB1, bitB1, 0);
      MAP_GPIOPinWrite(baseB2, bitB2, bitB2);
    }
    else
    {
      MAP_GPIOPinWrite(baseB1, bitB1, bitB1);
      MAP_GPIOPinWrite(baseB2, bitB2, 0);
    }
  }
  else
  {
    // Overflow interrupt
    HWREG(TIMERA0_BASE + TIMER_O_ICR) = 0x100;
    
    MAP_GPIOPinWrite(baseB1, bitB1, bitB1);
    MAP_GPIOPinWrite(baseB2, bitB2, bitB2);
  }
}

void setSpeed(int16_t left, int16_t right)
{
  if(left > 100)
  {
    speedLeft = 100;
  }
  else if(left < -100)
  {
    speedLeft = -100;
  }
  else
  {
    speedLeft = left;
  }
  
  if(right > 100)
  {
    speedRight = 100;
  }
  else if(right < -100)
  {
    speedRight = -100;
  }
  else
  {
    speedRight = right;
  }
  
  // set interrupt call speed
  uint32_t interruptLeft = (MOTOR_PRESCALER - MOTOR_OFFSET) * abs(speedLeft) / 100;
  uint32_t interruptRight = (MOTOR_PRESCALER - MOTOR_OFFSET) * abs(speedRight) / 100;
  
  MAP_TimerMatchSet(TIMERA0_BASE, TIMER_A, interruptLeft);
  MAP_TimerMatchSet(TIMERA0_BASE, TIMER_B, interruptRight);
}

void setup()
{
  #ifdef ENABLE_MOTORS
  motorSetup();
  #endif
  
  // initialize serial communication
  Serial.begin(115200);
  
  //pinMode(SDA, INPUT_PULLUP);
  //pinMode(SCL, INPUT_PULLUP);
  pinMode(LED, OUTPUT);
  
  // Initialize the 'Wire' class for the I2C-bus.
  Wire.begin();

  // Clear the 'sleep' bit to start the sensor.
  MPU9150_writeSensor(MPU9150_PWR_MGMT_1, 0);

  MPU9150_setupCompass();
  
  // Wi-Fi stuff

  // attempt to connect to Wifi network:
  /*Serial.print("Attempting to connect to Network named: ");
  // print the network name (SSID);
  Serial.println(ssid); 
  // Connect to WPA/WPA2 network. Change this line if using open or WEP network:
  WiFi.begin(ssid, password);
  while(WiFi.status() != WL_CONNECTED)
  {
    // print dots while we wait to connect
    Serial.print(".");
    delay(300);
  }
  
  Serial.println("\nYou're connected to the network");
  Serial.println("Waiting for an ip address");
  
  while(WiFi.localIP() == INADDR_NONE)
  {
    // print dots while we wait for an ip addresss
    Serial.print(".");
    delay(300);
  }

  // you're connected now, so print out the status  
  printWifiStatus();
  
  Serial.println("Starting webserver on port 80");
  server.begin();                           // start the web server on port 80
  Serial.println("Webserver started!");*/
}

void loop()
{
  Serial.println(MPU9150_readSensor(MPU9150_GYRO_XOUT_L,MPU9150_GYRO_XOUT_H));
  // Read accelerometer data
  //error = accelerometer.readZData();
  
  delay(100);
  
  /*Serial.println(error_avg);
  delay(100);*/
  
  // Do control stuff
  /*error = error - UPRIGHT_VALUE_ACCELEROMETER;
  
  memory[i] = error;
  i++;
  
  error_avg = 0;
  
  for(j=0;j<AVG;j++)
    error_avg += memory[j];
    
  error_avg /= AVG;
  
  if(i > AVG)
    i = 0;
  
  
  
  
  //integral = integral + error;
  derivate = error_avg - derivate;
  
  speed = error_avg * KP + derivate * KD;
  //speed = error * KP + integral * KI + derivate * KD;
  
  derivate = error;
  
  // Apply motor speeds
  
  setSpeed(speed, speed);
  //setSpeed(0, 0);
  delayMicroseconds(200);*/
  
  // min = 400
  // max = 3600
  /*for(int8_t i = -50; i < 50; i++)
  {
    //error = accelerometer.readXData();
    setSpeed(i, i);
    delay(100);
  }*/
  
  //webServer();
}

/*void webServer()
{
  // listen for incoming clients
  WiFiClient client = server.available();
  if(client)
  {
    Serial.println("new client");
    // an http request ends with a blank line
    boolean currentLineIsBlank = true;
    while(client.connected())
    {
      if(client.available())
      {
        char c = client.read();
        Serial.write(c);
        // if you've gotten to the end of the line (received a newline
        // character) and the line is blank, the http request has ended,
        // so you can send a reply
        if(c == '\n' && currentLineIsBlank)
        {
          // send a standard http response header
          client.println("HTTP/1.1 200 OK");
          client.println("Content-Type: text/html");
          client.println("Connection: close");  // the connection will be closed after completion of the response
          client.println("Refresh: 5");  // refresh the page automatically every 5 sec
          client.println();
          client.println("<!DOCTYPE HTML>");
          client.println("<html>");
          
          // output the value of each analog input pin
          for(int analogChannel = 0; analogChannel < 6; analogChannel++)
          {
            int sensorReading = analogChannel; //analogRead(analogChannel);
            client.print("analog input ");
            client.print(analogChannel);
            client.print(" is ");
            client.print(sensorReading);
            client.println("<br />");
          }
          client.println("</html>");
          break;
        }
        if(c == '\n')
        {
          // you're starting a new line
          currentLineIsBlank = true;
        }
        else if(c != '\r')
        {
          // you've gotten a character on the current line
          currentLineIsBlank = false;
        }
      }
    }
    // give the web browser time to receive the data
    delay(1);

    // close the connection:
    client.stop();
    Serial.println("client disonnected");
  }
}

void printWifiStatus()
{
  // print the SSID of the network you're attached to:
  Serial.print("Network Name: ");
  Serial.println(WiFi.SSID());

  // print your WiFi shield's IP address:
  IPAddress ip = WiFi.localIP();
  Serial.print("IP Address: ");
  Serial.println(ip);

  // print the received signal strength:
  long rssi = WiFi.RSSI();
  Serial.print("signal strength (RSSI):");
  Serial.print(rssi);
  Serial.println(" dBm");
}*/

// MPU-9150 Accelerometer + Gyro + Compass + Temperature
// -----------------------------
//
// By arduino.cc user "frtrobotik" (Tobias Hübner)
//
//
// July 2013
//      first version
//
// Open Source / Public Domain
//
// Using Arduino 1.0.1
// It will not work with an older version,
// since Wire.endTransmission() uses a parameter
// to hold or release the I2C bus.
//
// Documentation:
// - The InvenSense documents:
//   - "MPU-9150 Product Specification Revision 4.0",
//     PS-MPU-9150A.pdf
//   - "MPU-9150 Register Map and Descriptions Revision 4.0",
//     RM-MPU-9150A-00.pdf
//   - "MPU-9150 9-Axis Evaluation Board User Guide"
//     AN-MPU-9150EVB-00.pdf
//
// The accuracy is 16-bits.
//
// Some parts are copied by the MPU-6050 Playground page.
// playground.arduino.cc/Main/MPU-6050
// There are more Registervalues. Here are only the most
// nessecary ones to get started with this sensor.

//http://pansenti.wordpress.com/2013/03/26/pansentis-invensense-mpu-9150-software-for-arduino-is-now-on-github/
//Thank you to pansenti for setup code.
//I will documented this one later.
void MPU9150_setupCompass(){
  MPU9150_I2C_ADDRESS = 0x0C;      //change Adress to Compass

  MPU9150_writeSensor(0x0A, 0x00); //PowerDownMode
  MPU9150_writeSensor(0x0A, 0x0F); //SelfTest
  MPU9150_writeSensor(0x0A, 0x00); //PowerDownMode

  MPU9150_I2C_ADDRESS = 0x68;      //change Adress to MPU

  MPU9150_writeSensor(0x24, 0x40); //Wait for Data at Slave0
  MPU9150_writeSensor(0x25, 0x8C); //Set i2c address at slave0 at 0x0C
  MPU9150_writeSensor(0x26, 0x02); //Set where reading at slave 0 starts
  MPU9150_writeSensor(0x27, 0x88); //set offset at start reading and enable
  MPU9150_writeSensor(0x28, 0x0C); //set i2c address at slv1 at 0x0C
  MPU9150_writeSensor(0x29, 0x0A); //Set where reading at slave 1 starts
  MPU9150_writeSensor(0x2A, 0x81); //Enable at set length to 1
  MPU9150_writeSensor(0x64, 0x01); //overvride register
  MPU9150_writeSensor(0x67, 0x03); //set delay rate
  MPU9150_writeSensor(0x01, 0x80);

  MPU9150_writeSensor(0x34, 0x04); //set i2c slv4 delay
  MPU9150_writeSensor(0x64, 0x00); //override register
  MPU9150_writeSensor(0x6A, 0x00); //clear usr setting
  MPU9150_writeSensor(0x64, 0x01); //override register
  MPU9150_writeSensor(0x6A, 0x20); //enable master i2c mode
  MPU9150_writeSensor(0x34, 0x13); //disable slv4
}

////////////////////////////////////////////////////////////
///////// I2C functions to get easier all values ///////////
////////////////////////////////////////////////////////////

int MPU9150_readSensor(int addrL, int addrH){
  Wire.beginTransmission(MPU9150_I2C_ADDRESS);
  Wire.write(addrL);
  Wire.endTransmission(false);

  Wire.requestFrom(MPU9150_I2C_ADDRESS, 1, true);
  byte L = Wire.read();

  Wire.beginTransmission(MPU9150_I2C_ADDRESS);
  Wire.write(addrH);
  Wire.endTransmission(false);

  Wire.requestFrom(MPU9150_I2C_ADDRESS, 1, true);
  byte H = Wire.read();

  return (int16_t)((H<<8)+L);
}

int MPU9150_readSensor(int addr){
  Wire.beginTransmission(MPU9150_I2C_ADDRESS);
  Wire.write(addr);
  Wire.endTransmission(false);

  Wire.requestFrom(MPU9150_I2C_ADDRESS, 1, true);
  return Wire.read();
}

int MPU9150_writeSensor(int addr,int data){
  Wire.beginTransmission(MPU9150_I2C_ADDRESS);
  Wire.write(addr);
  Wire.write(data);
  Wire.endTransmission(true);

  return 1;
}

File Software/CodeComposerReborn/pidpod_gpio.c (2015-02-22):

#include <stdint.h>

#include "pidpod_gpio.h"

/* Driverlib includes */
#include "hw_types.h"
#include "hw_timer.h"
#include "prcm.h"
#include "pin.h"
#include "hw_memmap.h"
#include "rom_map.h"
#include "gpio.h"
#include "hw_gpio.h"
#include "hw_adc.h"
#include "adc.h"

/* Common interface includes */
#include "gpio_if.h"

/* Gloab variables */
unsigned char pin_rled, pin_bled, pin_dip1, pin_dip2, pin_dip3, pin_dip4, pin_odo1, pin_odo2;
unsigned int port_rled, port_bled, port_dip1, port_dip2, port_dip3, port_dip4, port_odo1, port_odo2;

/* Pin definitions */
#define RLED    PIN_64
#define BLED	PIN_61
#define DIP4    PIN_18
#define DIP3    PIN_08
#define DIP2    PIN_45
#define DIP1    PIN_07
#define ODO1    PIN_06
#define ODO2    PIN_59
#define AISEN	PIN_57
#define BISEN	PIN_58
#define RLEDx   9
#define BLEDx	6
#define DIP4x   28
#define DIP3x   17
#define DIP2x   31
#define DIP1x   16
#define ODO1x   15
#define ODO2x   4
#define AISENx	ADC_CH_0
#define BISENx	ADC_CH_1

void InitGPIO(void)
{
	/* Activate GPIO clock per port. Not sure of which ports we use, so enable everything */
	MAP_PRCMPeripheralClkEnable(PRCM_GPIOA0, PRCM_RUN_MODE_CLK);
	MAP_PRCMPeripheralClkEnable(PRCM_GPIOA1, PRCM_RUN_MODE_CLK);
	MAP_PRCMPeripheralClkEnable(PRCM_GPIOA2, PRCM_RUN_MODE_CLK);
	MAP_PRCMPeripheralClkEnable(PRCM_GPIOA3, PRCM_RUN_MODE_CLK);
	MAP_PRCMPeripheralClkEnable(PRCM_GPIOA4, PRCM_RUN_MODE_CLK);

    /* Configure UART pins */
    MAP_PinTypeUART(PIN_55, PIN_MODE_3);
    MAP_PinTypeUART(PIN_57, PIN_MODE_3);

    /* Configure I2C pins */
    MAP_PinTypeI2C(PIN_01, PIN_MODE_1);
    MAP_PinTypeI2C(PIN_02, PIN_MODE_1);

    /* COngifure current sense ADC inputs */
    MAP_PinTypeADC(AISEN,PIN_MODE_255);
    MAP_PinTypeADC(BISEN,PIN_MODE_255);
    MAP_ADCChannelEnable(ADC_BASE, AISENx);
    MAP_ADCChannelEnable(ADC_BASE, BISENx);
    MAP_ADCEnable(ADC_BASE);

	/* Set pin mode for DIP and LED pins */
	MAP_PinTypeGPIO(RLED, PIN_MODE_0, false);
	MAP_PinTypeGPIO(BLED, PIN_MODE_0, false);
	MAP_PinTypeGPIO(DIP1, PIN_MODE_0, false);
	MAP_PinTypeGPIO(DIP2, PIN_MODE_0, false);
	MAP_PinTypeGPIO(DIP3, PIN_MODE_0, false);
	MAP_PinTypeGPIO(DIP4, PIN_MODE_0, false);
	MAP_PinTypeGPIO(ODO1, PIN_MODE_0, false);
	MAP_PinTypeGPIO(ODO2, PIN_MODE_0, false);

	/* Get port name and bin number from GPIO number (TI lookup table) LED, DIP, ODO */
	GPIO_IF_GetPortNPin(RLEDx, &port_rled, &pin_rled);
	GPIO_IF_GetPortNPin(BLEDx, &port_bled, &pin_bled);
	GPIO_IF_GetPortNPin(DIP1x, &port_dip1, &pin_dip1);
	GPIO_IF_GetPortNPin(DIP2x, &port_dip2, &pin_dip2);
	GPIO_IF_GetPortNPin(DIP3x, &port_dip3, &pin_dip3);
	GPIO_IF_GetPortNPin(DIP4x, &port_dip4, &pin_dip4);
	GPIO_IF_GetPortNPin(ODO1x, &port_odo1, &pin_odo1);
	GPIO_IF_GetPortNPin(ODO2x, &port_odo2, &pin_odo2);

	/* Set pin direction LED, DIP, ODO */
	GPIODirModeSet(port_rled, pin_rled, 1);
	GPIODirModeSet(port_bled, pin_bled, 1);
	GPIODirModeSet(port_dip1, pin_dip1, 0);
	GPIODirModeSet(port_dip2, pin_dip2, 0);
	GPIODirModeSet(port_dip3, pin_dip3, 0);
	GPIODirModeSet(port_dip4, pin_dip4, 0);
	GPIODirModeSet(port_odo1, pin_odo1, 0);
	GPIODirModeSet(port_odo2, pin_odo2, 0);
}

uint8_t readDIP1(void)
{
	return (uint8_t)GPIO_IF_Get(DIP1x, port_dip1, pin_dip1);
}

uint8_t readDIP2(void)
{
	return (uint8_t)GPIO_IF_Get(DIP2x, port_dip2, pin_dip2);
}

uint8_t readDIP3(void)
{
	return (uint8_t)GPIO_IF_Get(DIP3x, port_dip3, pin_dip3);
}

uint8_t readDIP4(void)
{
	return (uint8_t)GPIO_IF_Get(DIP4x, port_dip4, pin_dip4);
}

uint8_t readODO1(void)
{
	return (uint8_t)GPIO_IF_Get(ODO1x, port_odo1, pin_odo1);
}

uint8_t readODO2(void)
{
	return (uint8_t)GPIO_IF_Get(ODO2x, port_odo2, pin_odo2);
}

void setRLED(void)
{
	GPIO_IF_Set(RLEDx, port_rled, pin_rled, 1);
}

void clearRLED(void)
{
	GPIO_IF_Set(RLEDx, port_rled, pin_rled, 0);
}

void setBLED(void)
{
	GPIO_IF_Set(BLEDx, port_bled, pin_bled, 1);
}

void clearBLED(void)
{
	GPIO_IF_Set(BLEDx, port_bled, pin_bled, 0);
}

uint16_t readAISEN(void)
{
    unsigned long sample = 0;

    /* ADC measurement */
    if(MAP_ADCFIFOLvlGet(ADC_BASE, AISENx))
	{
		sample = MAP_ADCFIFORead(ADC_BASE, AISENx);
		sample = sample >> 2;
		sample &= 0x0FFF;
	}

	return (uint16_t)(sample);
}

uint16_t readBISEN(void)
{
    unsigned long sample = 0;

    /* ADC measurement */
	if(MAP_ADCFIFOLvlGet(ADC_BASE, BISENx))
	{
		sample = MAP_ADCFIFORead(ADC_BASE, BISENx);
		sample = sample >> 2;
		sample &= 0x0FFF;
	}

	return (uint16_t)(sample);
}

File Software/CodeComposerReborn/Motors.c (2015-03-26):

/* Standard include */
#include <stdint.h>
#include <math.h>

#include "Motors.h"

/* Driverlib includes */
#include "hw_types.h"
#include "hw_timer.h"
#include "hw_ints.h"
#include "prcm.h"
#include "timer.h"
#include "pin.h"
#include "hw_memmap.h"
#include "rom_map.h"
#include "gpio.h"
#include "hw_gpio.h"
#include "interrupt.h"
#include "hw_apps_rcm.h"
#include "hw_common_reg.h"
#include "rom.h"
#include "rom_map.h"
#include "timer.h"
#include "utils.h"

/* Common interface includes */
#include "timer_if.h"
#include "gpio_if.h"

/* GLOBALS */
unsigned int port_ain1, port_ain2, port_bin1, port_bin2;
unsigned char pin_ain1, pin_ain2, pin_bin1, pin_bin2;
uint8_t bitA1, bitA2, bitB1, bitB2;

int8_t speedLeft = 0;
int8_t speedRight = 0;

/* DEFINES */

#define AIN1	PIN_50
#define AIN2	PIN_53
#define BIN1	PIN_63 // NEW VERSION
//#define BIN1	PIN_62 // TI version
#define BIN2	PIN_05
#define AIN1x	0
#define AIN2x	30
 #define BIN1x	8 // new version
//#define BIN1x	7 // TI version
#define BIN2x	14
#define MOTOR_PRESCALER 8000
#define MOTOR_OFFSET 400




void motorSetup()
{
	/* Set pin mode for Hbridge output pins */
	MAP_PinTypeGPIO(AIN1, PIN_MODE_0, false); /* Ain 1 */
	MAP_PinTypeGPIO(AIN2, PIN_MODE_0, false); /* Bin 1 */
	MAP_PinTypeGPIO(BIN1, PIN_MODE_0, false);  /* Bin 2 */
	MAP_PinTypeGPIO(BIN2, PIN_MODE_0, false); /* Ain 2 */

	/* Get port name and bin number from GPIO number (TI lookup table) */
	GPIO_IF_GetPortNPin(AIN1x, &port_ain1, &pin_ain1);
	GPIO_IF_GetPortNPin(AIN2x, &port_ain2, &pin_ain2);
	GPIO_IF_GetPortNPin(BIN1x, &port_bin1, &pin_bin1);
	GPIO_IF_GetPortNPin(BIN2x, &port_bin2, &pin_bin2);

	/* Set pin direction */
	GPIODirModeSet(port_ain1, pin_ain1, 1);
	GPIODirModeSet(port_ain2, pin_ain2, 1);
	GPIODirModeSet(port_bin1, pin_bin1, 1);
	GPIODirModeSet(port_bin2, pin_bin2, 1);

	/* Set value to write to PIN */
	bitA1 = 1 << (AIN1x % 8);
	bitA2 = 1 << (AIN2x % 8);
	bitB1 = 1 << (BIN1x % 8);
	bitB2 = 1 << (BIN2x % 8);

	// Enable timer A peripheral
	MAP_PRCMPeripheralClkEnable(PRCM_TIMERA0, PRCM_RUN_MODE_CLK);
	MAP_PRCMPeripheralReset(PRCM_TIMERA0);

	// Split channels and configure for periodic interrupts
	MAP_TimerConfigure(TIMERA0_BASE, TIMER_CFG_SPLIT_PAIR | TIMER_CFG_A_PERIODIC | TIMER_CFG_B_PERIODIC);
	MAP_TimerPrescaleSet(TIMERA0_BASE, TIMER_A, 0);
	MAP_TimerPrescaleSet(TIMERA0_BASE, TIMER_B, 0);

	// Set compare interrupt
	MAP_TimerIntEnable(TIMERA0_BASE, TIMER_TIMA_MATCH);
	MAP_TimerIntEnable(TIMERA0_BASE, TIMER_TIMB_MATCH);

	// Configure compare interrupt, start with 0 speed
	MAP_TimerMatchSet(TIMERA0_BASE, TIMER_A, 0);
	MAP_TimerMatchSet(TIMERA0_BASE, TIMER_B, 0);

	// Set timeout interrupt
	MAP_TimerIntRegister(TIMERA0_BASE, TIMER_A, TimerBaseIntHandlerA);
	MAP_TimerIntRegister(TIMERA0_BASE, TIMER_B, TimerBaseIntHandlerB);
	MAP_TimerIntEnable(TIMERA0_BASE, TIMER_TIMA_TIMEOUT);
	MAP_TimerIntEnable(TIMERA0_BASE, TIMER_TIMB_TIMEOUT);

	// Turn on timers
	MAP_TimerLoadSet(TIMERA0_BASE, TIMER_A, MOTOR_PRESCALER);
	MAP_TimerLoadSet(TIMERA0_BASE, TIMER_B, MOTOR_PRESCALER);

	MAP_TimerEnable(TIMERA0_BASE, TIMER_A);
	MAP_TimerEnable(TIMERA0_BASE, TIMER_B);
}

void TimerBaseIntHandlerA(void)
{
	if(HWREG(TIMERA0_BASE + TIMER_O_MIS) & 0x10)
	{
		// Match interrupt
		HWREG(TIMERA0_BASE + TIMER_O_ICR) = 0x10;
		if(speedLeft > 0)
		{
			MAP_GPIOPinWrite(port_ain1, pin_ain1, 0);
			MAP_GPIOPinWrite(port_ain2, pin_ain2, bitA2);
		}
		else
		{
			MAP_GPIOPinWrite(port_ain1, pin_ain1, bitA1);
			MAP_GPIOPinWrite(port_ain2, pin_ain2, 0);
		}
	}
	else
	{
		// Overflow interrupt
		HWREG(TIMERA0_BASE + TIMER_O_ICR) = 0x1;
		MAP_GPIOPinWrite(port_ain1, pin_ain1, bitA1);
		MAP_GPIOPinWrite(port_ain2, pin_ain2, bitA2);
	}
}

void TimerBaseIntHandlerB(void)
{
	if(HWREG(TIMERA0_BASE + TIMER_O_MIS) & 0x800)
	{
		// Match interrupt
		HWREG(TIMERA0_BASE + TIMER_O_ICR) = 0x800;
		if(speedRight > 0)
		{
			MAP_GPIOPinWrite(port_bin1, pin_bin1, 0);
			MAP_GPIOPinWrite(port_bin2, pin_bin2, bitB2);
		}
		else
		{
			MAP_GPIOPinWrite(port_bin1, pin_bin1, bitB1);
			MAP_GPIOPinWrite(port_bin2, pin_bin2, 0);
		}
	}
	else
	{
	  // Overflow interrupt
	  HWREG(TIMERA0_BASE + TIMER_O_ICR) = 0x100;

	  MAP_GPIOPinWrite(port_bin1, pin_bin1, bitB1);
	  MAP_GPIOPinWrite(port_bin2, pin_bin2, bitB2);
	}
}

void setSpeed(int16_t left, int16_t right)
{
	if(left > 100)
	{
		speedLeft = 100;
	}
	else if(left < -100)
	{
		speedLeft = -100;
	}
	else
	{
		speedLeft = left;
	}

	if(right > 100)
	{
		speedRight = 100;
	}
	else if(right < -100)
	{
		speedRight = -100;
	}
	else
	{
		speedRight = right;
	}

	// set interrupt call speed
	uint32_t interruptLeft = (MOTOR_PRESCALER - MOTOR_OFFSET) * abs(speedLeft) / 100;
	uint32_t interruptRight = (MOTOR_PRESCALER - MOTOR_OFFSET) * abs(speedRight) / 100;

	MAP_TimerMatchSet(TIMERA0_BASE, TIMER_A, interruptLeft);
	MAP_TimerMatchSet(TIMERA0_BASE, TIMER_B, interruptRight);
}

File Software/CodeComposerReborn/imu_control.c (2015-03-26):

#include <math.h>
#include <stdint.h>

#include "imu_control.h"
#include "pidpod_gpio.h"
#include "Motors.h"
#include "odometer.h"

#include "hw_memmap.h"
#include "hw_types.h"
#include "hw_timer.h"
#include "rom_map.h"
#include "prcm.h"
#include "timer.h"
#include "MPU9150.h"


/* --------------- Controller constants ----------------- */
#define IMU_CONTROLLER_STARTUP	 	8000 	// depends on the period. Target period is 100Hz
#define IMU_CONTROLLER_PRESCALER	100   	// clock frequency is now 800KHz

/* Other constants */
const float NSAMPLES = 16;
const float COMPLEMENTARY_GYRO = 0.98;
const float COMPLEMENTARY_ACC = 0.02;
const float CPERIOD = 100;
const float INTEGRAL_ADD = 0.1;
const float GYRO_NORM = 200;
const float ACC_NORM = 1000;
const float PID_ARW = 4;
const float ADC_MULTIPLIER = 1.46/4096;//1.46 V is 4096 in the ADC
const float CURRENT_RELATION = 10000; // from the ADC voltage U = RI, so I = U/R, R = 0.1ohm, hence *10'000 to have the current in mAmpere
const float ROUNDED_MULTIPLIER = 3.55;

/* ------------- Library local variables ---------------- */
float integral = 0;
float gyro_offset;
float accelerometer;
float upright_value_accelerometer, safe_restart_acc;
float acc_reading;
float gyro_angle;
float angle = 0;
int16_t speed = 0;
float Kp,Ki,Kd;	// again, why not recognized? energia/arduino weird stuff? They should be GLOBAL! :/ Still throws an error during compilation if ki,kp,kd instead of Kp,Ki,Kd
uint16_t current_1;
uint16_t current_2;




/* --------------------- Functions ----------------------- */
void imu_setup(void)
{
	uint8_t i;


	MPU9150_init();

	// gyroscope offset

	// Find accelerometer and gyroscope offset
	accelerometer = 0;
	gyro_offset = 0;
	for(i = 0; i < NSAMPLES; i++)
	{
	accelerometer += (float)MPU9150_readSensor_2byte(MPU9150_ACCEL_ZOUT_L, MPU9150_ACCEL_ZOUT_H);
	gyro_offset += (float)MPU9150_readSensor_2byte(MPU9150_GYRO_XOUT_L, MPU9150_GYRO_XOUT_H);
	}
	// average
	upright_value_accelerometer = accelerometer/NSAMPLES;
	safe_restart_acc = upright_value_accelerometer;
	gyro_offset /= NSAMPLES;
}




void controller_setup(){
	// Enable timer A peripheral
  	MAP_PRCMPeripheralClkEnable(PRCM_TIMERA1, PRCM_RUN_MODE_CLK);
  	MAP_PRCMPeripheralReset(PRCM_TIMERA1);
  	
  	// Configure one channel for periodic interrupts
  	MAP_TimerConfigure(TIMERA1_BASE, TIMER_CFG_SPLIT_PAIR | TIMER_CFG_A_PERIODIC);
  	MAP_TimerPrescaleSet(TIMERA1_BASE, TIMER_A, IMU_CONTROLLER_PRESCALER);
	
  	// Set timeout interrupt
  	MAP_TimerIntRegister(TIMERA1_BASE, TIMER_A, ControllerIntHandler);
  	MAP_TimerIntEnable(TIMERA1_BASE, TIMER_TIMA_TIMEOUT);

  	// Turn on timers
  	MAP_TimerLoadSet(TIMERA1_BASE, TIMER_A, IMU_CONTROLLER_STARTUP); 
  	MAP_TimerEnable(TIMERA1_BASE, TIMER_A);
}




/* Reads the IMU, but only the variables that are interesting for the segway
control loop */
void read_segway_imu(void)
{
	upright_value_accelerometer = get_accelerometer_offset();
	acc_reading = -(MPU9150_readSensor_2byte(MPU9150_ACCEL_ZOUT_L, MPU9150_ACCEL_ZOUT_H) - upright_value_accelerometer) / ACC_NORM;
  	gyro_angle = (MPU9150_readSensor_2byte(MPU9150_GYRO_XOUT_L, MPU9150_GYRO_XOUT_H) - gyro_offset) / GYRO_NORM;
}




/* Controller Interrupt routine */
void ControllerIntHandler(void)
{
    /* Clear interrupt flag */
    HWREG(TIMERA1_BASE + TIMER_O_ICR) = 0x1; 
    
    /* Get sensors */
    read_segway_imu();
  
  	/* Compute error between desired angle (0) and the real angle with complementary filter */
  	angle = (angle + gyro_angle / CPERIOD) * COMPLEMENTARY_GYRO + (acc_reading * COMPLEMENTARY_ACC); // / 100 is the period of the controller in milliseconds

  	/* Accumulate integral error */
  	integral = integral + angle * INTEGRAL_ADD;

  	/* Apply ARW protection */
  	if(integral > PID_ARW)
  	  integral = PID_ARW;
  	else if(integral < -PID_ARW)
  	  integral = -PID_ARW;

  	/* Compute controller speed */
  	speed = angle * Kp + integral * Ki + gyro_angle * Kd;
  	
  	/* Sense motor current */
  	current_1 = readAISEN();
  	current_2 = readBISEN();

  	
  	
  	/* Apply command value to the motors (as long as the DIP4 is = 1) */
  	if(readDIP4() && angle_acceptable())
  	//if(readDIP4())
    	setSpeed(speed, speed);

  	else
		setSpeed(0, 0);
}



float get_accelerometer_default(void)
{
	return accelerometer;
}

int16_t get_speed(void)
{
	return  speed;
}

void set_controller_parameters(float p, float i, float d)
{
	Kp = p;
	Ki = i;
	Kd = d;
}
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

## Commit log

2014-11-28 PWM working
    PWM mode implemented through interruptions on timer 0, channels A and B.
    Timeout (overflow) interruption turn on the motor
    Match (compare) interruption turn off the motor
    Changes in the configuration of the GPIO pins
    Changes in the configurations of the timers and interruptions
2014-11-30 Added 3D printable mechanical base
    [Assembly.SLDASM, Base.SLDPRT, Base.STL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]
2014-12-03 PWM pin toggle with TI commands for faster output
2014-12-08 Added electronics documentation
    Schematics, PCD documentation and Gerber fabrication files
    [sbp_pcb.GBL, sbp_pcb.GBS, sbp_pcb.GM1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]
2014-12-08 New base design
    [Assembly2.SLDASM, Assembly3.SLDASM, Base_v2.SLDPRT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]
2014-12-08 Moved electronics to Electronics folder
    [sbp_pcb.GBL, sbp_pcb.GBS, sbp_pcb.GM1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]
2014-12-08 Revert "Update documentaion"
    This reverts commit 39f66eaa568c8655f730c1eeb12607631fffb33e.
    [PIDPOD5.ino]
2014-12-08 Revert "Revert "Update documentaion""
    This reverts commit da7d658748cbe7e410e5a71177a0268953b5b81c.
    [PIDPOD5.ino]
2014-12-10 Made Wi-Fi selectable via DIP switch
2015-01-30 Extracted IMU setup in an external library
    The IMU is no more initialized in a messy way inside the setup()
    function, but is now a function belonging to an “ad hohoc” library
2015-01-30 Cleaned out IMU control part
    Now all functions regarding the IMU are placed inside the imu_control
    library
2015-01-30 Controller put in an interrupt
    The controller part is put in an interrupt routine inside the
    “imu_control” library.
    Pay attention that the library timer is not yet correctly setup, refer
    to the datasheet to complete it
    [PIDPOD7.ino]
2015-01-30 Major changes in PIDPOD7
    PIDPOD7 was wrongly based on PIDPOD6 instead of PIDPOD5.
    Changes have been made to match PIDPOD7 to PIDPOD5. There is no chance
    this will work, so an heavy debug session is required.
    Moreover, the controller interrupt is still not set up
    [PIDPOD7.ino]
2015-01-30 Compiler error corrected
    Still, debug the swag way (does it still keep upright?)
    But BEFORE that, set up properly de controller interrupt routine
    timings and the rest of the settings
    [PIDPOD7.ino]
2015-01-31 Mechanical upgrade
    This will allow to place encoders on the PIDPOD base
    [Assembly.SLDASM, Assembly2.SLDASM, Assembly3.SLDASM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]
2015-01-31 Controll interrupt routine set up
    Set a proper prescaler (which by the way is probably NOT a prescaler,
    but the start of the contdown)
2015-01-31 Bugs corrected in the controller interrupt routine
    The IMU controller now properly runs within an interrupt routine at
    100Hz
    [PIDPOD7.ino]
2015-01-31 updated imu_controller library
2015-01-31 Killed some more interrupt_controller bugs
2015-01-31 Mechanical odometers corrections
    Changed some dimensions to have better working encoders
    [Assembly3.SLDASM, IR_holder.SLDPRT]
2015-01-31 Minor changes and NEW odometry library
    Minor changes in preparation for the implementation of odometry.
    New ODOMETRY library. Not yet functional
2015-02-01 Odometry ok
    Odometer is implemented but not yet correctly working (the controller
    does not work)
    There is a wi-fi related problem at :
    WiFiClient client = server.available();
    It often crashes the whole uC
    [PIDPOD7.ino]
2015-02-01 Stability update
    The WiFI does not crash the CC3200 anymore.
    Nonetheless, the WiFi does not work because of Energia embedded
    functions bugs:
    https://github.com/energia/Energia/issues/545
    [PIDPOD7.ino]
2015-02-01 Libraries update
    Minors updates of the odometer library and imu_control
2015-02-02 Better control
    PI controller on odometry, regulated in speed. Distance is integrated
    (and multiplied with the KI term).
    Must add some kind of odometer reset, since now the PIDPOD is stable
    only in a particular point on a straight line.
    Maybe add odometry_total*KI to the acc_value when the PIDPOD is fairly
    stable and then reset odometry_total to 0?
    The wifi is still buggy! Do not use wifi
    [PIDPOD7.ino]
2015-02-03 Mechanical change in the odometer wheel
    Better suits the mechanical dimension of the rest of the PIDPOD
    [odometer3D.SLDPRT]
2015-02-06 Added STL files
    Now it is possible to just print out the segway with a 3D printer
    [Assembly3.SLDASM, Base_v3.STL, IR_holder.STL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]
2015-02-10 Back to CodeComposerStudio for better HTTP server implementation
    Translating the code to work with CCS instead of Energia.
    The goal is to have a better http wifi server.
    The code is not working now
    [MPU9150.c, Motors.c, imu_control.c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]
2015-02-19 Replaced float #define with const float
    Apparently the CCS compiler does not like the definition of constants
    ant their interaction with float.
    No time to investigate, replaced all defines interacting with float with
    const float even if the SRAM will not be happy.
    Some replacement may have escaped (especially in odometer and main)
    [MPU9150.c, Motors.c, imu_control.c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]
2015-02-20 Finished fixing the float define issue
    [main.c, odometer.c]
2015-02-20 User can now set the controller parameters through a web interface
    Connect to PIDPODlinkmain and type:
    mysimplelink.net/led_demo.html
    led_demo should be replaced with another name
    Sending data to the web interface is not yet working properly
    [imu_control.c, main.c, odometer.c]
2015-02-21 Improved (mechanical) stability
    Control frequency for odometers from 10 to 5 Hz
    Angle controller parameters:
    Kp : 20
    Ki: 25
    Kd: 0.5
    Speed controller parameters:
    Kp: 100
    Ki: 3
    Kd: 50
    [main.c, odometer.c]
2015-02-22 Energia sketch mechanical stability update
    [PIDPOD7.ino]
2015-02-22 PIDPOD stable release
    Connect to
    PIDPODlinkmain
    Enter
    http://mysimplelink.net/pidpod.html
    On the PIDPOD, start with the bottom switch not switched, switch it
    while holding it at the equilibrium to start the program (RED LED should
    go off)
    One issue remaining, the .bin does not execute automatically when the
    PIDPOD is turned on (even with the SOP23 jumper removed)
    [Motors.c, imu_control.c, main.c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]
2015-02-22 Added safety stop
    If the segway lean angle is to grate for >0.5s the motors stop.
    One can then put it at the point of equilibrium again and toggle the
    second DIP switch from the bottom to restart the execution of the
    program
2015-03-26 Works withouth debug mode
    Do not forget to switch the comments on the lines in
    motors.c
